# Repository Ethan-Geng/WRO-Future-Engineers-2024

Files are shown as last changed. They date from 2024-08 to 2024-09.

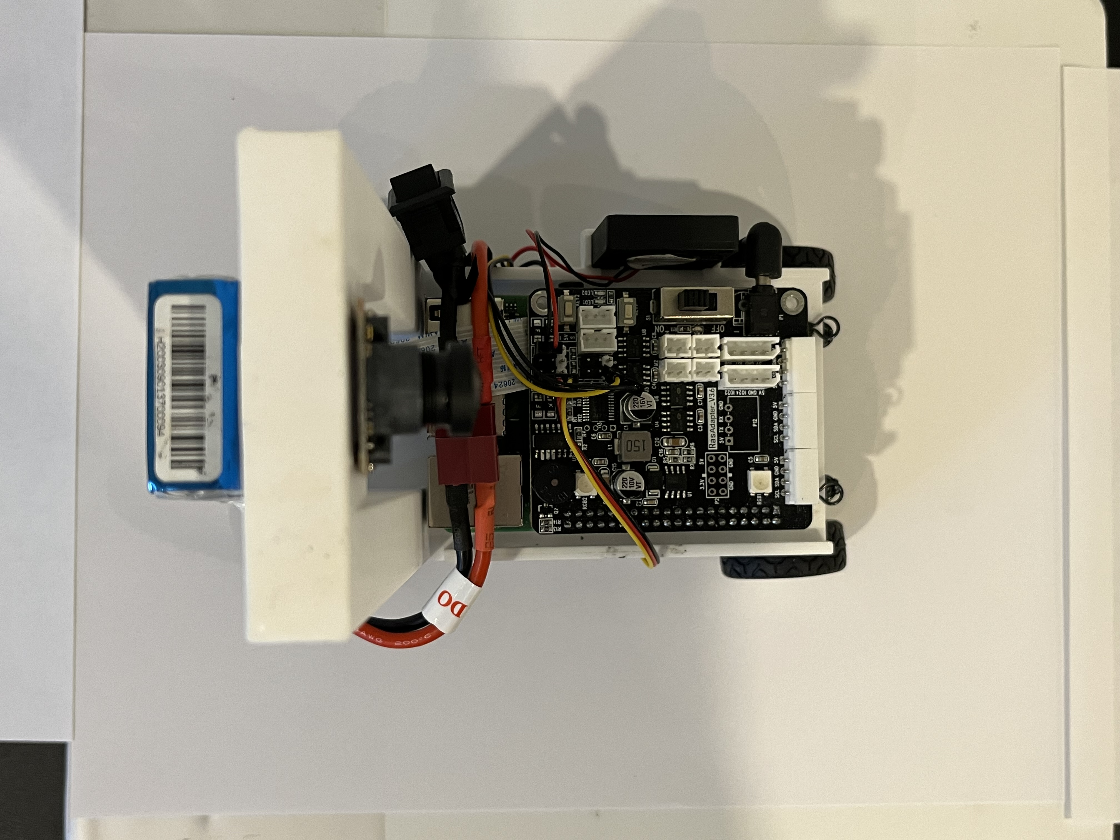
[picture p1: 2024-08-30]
v-photos/Car_Top_View.jpg

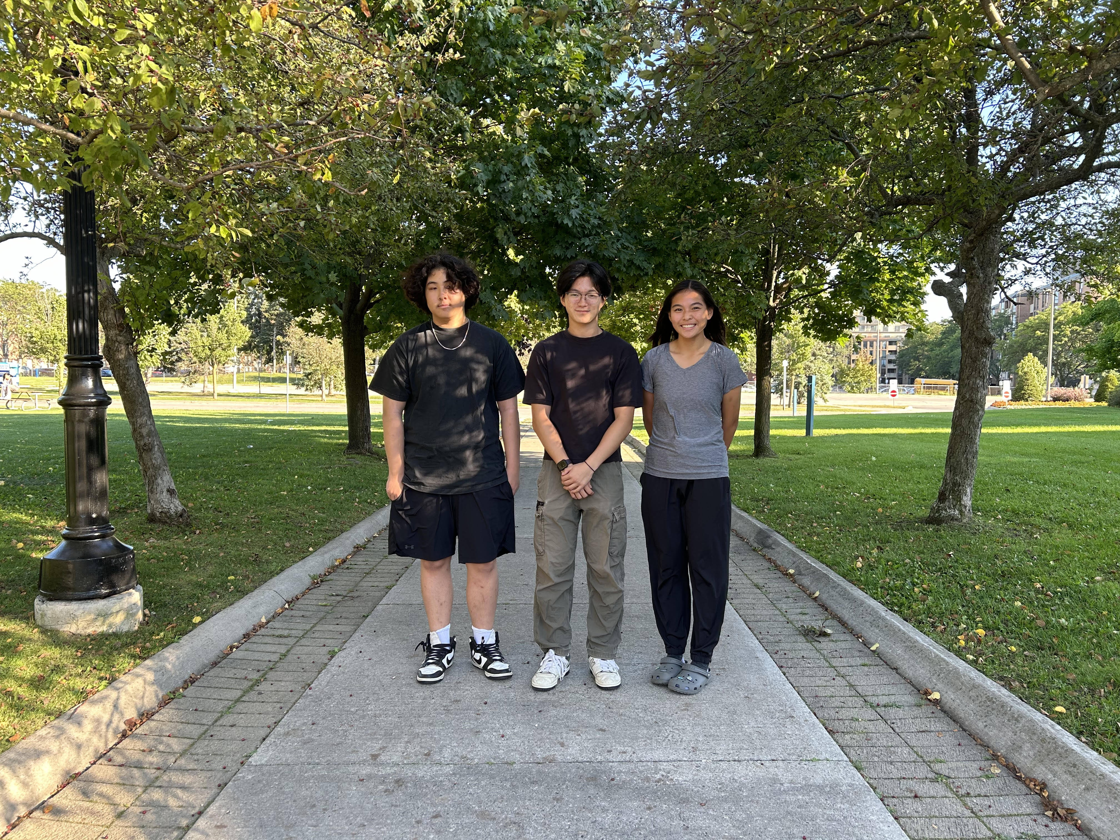
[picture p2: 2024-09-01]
t-photos/Official_Photo.jpg

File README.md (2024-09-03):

Documentation l Explorer Robotics l Team French Fries
====
## Introduction
This repository contains the engineering process of Team French Fries' self-driven vehicle's model participating in the WRO Future Engineers competition in the season 2024. Included in the repository are materials used, schematics, pictures, and software.

## Team Members
* Ethan Geng (EMAIL: ethan.geng7@gmail.com)
* Alexandra Chao-Lau (EMAIL: alexandra.clau3@gmail.com)
* Kenneth Mac (EMAIL: kennethmacrobotics@gmail.com)

## Content

* `t-photos` contains 2 photos of the team (an official one and one funny photo with all team members)
* `v-photos` contains 6 photos of the vehicle (from every side, from top and bottom)
* `video` contains the video.md file with the link to a video where driving demonstration exists
* `schemes` contains one or several schematic diagrams in form of JPEG, PNG or PDF of the electromechanical components illustrating all the elements (electronic components and motors) used in the vehicle and how they connect to each other.
* `src` contains code of control software for all components which were programmed to participate in the competition
* `models` is for the files for models used by 3D printers, laser cutting machines and CNC machines to produce the vehicle elements. If there is nothing to add to this location, the directory can be removed.
* `other` is for other files which can be used to understand how to prepare the vehicle for the competition. It may include documentation how to connect to a SBC/SBM and upload files there, datasets, hardware specifications, communication protocols descriptions etc. If there is nothing to add to this location, the directory can be removed.

## Parts List & Design Choice

| Part  | Description  | Photo  |
|:---|:---|:---|
| __Carisma Puma Hybrid Rally RC Car 1/24 AWD ([Link](https://carisma-shop.com/products/gt24-m-sport-2022-puma-hybrid-rally1))__ | Equipped with a lightweight chassis, high traction tires, and effective friction dampeners, this RC car serves as a perfect base for our team to construct our self-driving car using. With the addition of the parking lot in this year's competition, we chose this 1/24th scale size as its dimensions allow us to effectively utilize back-in parking, as opposed to parallel parking. This not only saves time, but minimizes chances of error during our parking phase of Obstacle Challenge. | Rally Car Chassis |
| __Raspberry Pi 4 Model B ([Link](https://www.raspberrypi.com/products/raspberry-pi-4-model-b/))__ | We chose the Raspberry Pi to act as the brain of the entire car. The code on the board handles all computing aspects, including the image processing and control signals. It's 64-bit quad-core processor coupled with 8GB of Random Access Memory (RAM) ensures fast processing of our code. | Raspberry Pi 4 Model B |
| __Hiwonder Pi Expansion Board (N/A)__ | Compact and practical, the expansion board stacks on top of our Raspberry Pi board and is attached using the board's universal input/output pins. This expansion board allows for easy connections for our servo motor, brushless motor, and Pi fan. | N/A |
| __SainSmart MIPI CSI Fisheye Camera Module ([Link](https://www.sainsmart.com/products/noir-wide-angle-fov160-5-megapixel-camera-module))__ | This CSI camera conveniently connects to our Raspberry Pi board's camera module port and offers a wide 160 degree viewing angle with great 5MP resolution, colour quality, and a high frame rate. This camera is responsible for detecting walls, obstacles, and lines. | MIPI Camera |
| __Micro Servo Motor ([Link](https://ca.robotshop.com/products/hs-5055mg-metal-gear-micro-servo-motor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))__ | This programmable micro servo motor allows our team to precisely control the steering angle of our car. It's compact and lightweight design ensures that it can fit perfectly within our car chassis. | Servo Motor |
| __GeeekPi Pi Fan ([Link](https://www.amazon.ca/GeeekPi-Raspberry-Radiator-Aluminum-Heatsinks/dp/B07C9C99RM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))__ | We decided to include this efficient fan to effectively cool and dissipate heat from our Raspberry Pi, which will help to mitigate thermal throttling and thereby improve performance under a heavy processing load. Our team found that the addition of this Pi fan can cool the Raspberry Pi up to 30 degrees celsius. | Pi Fan |
| __Furitek Komodo Micro Brushless Motor + ESC ([Link](https://furitek.com/products/furitek-stinger-brushless-power-system-for-scx24))__ | The Furitek brushless motor works with the spur gear in our car chassis to drive the wheels. It has a lightweight but powerful design that provides smooth driving with great speed, high torque, and zero cogging. We chose to use a brushless motor because of the increased efficiency due to the eliminaton of brushes which create friction, greater reliablilty, and overall improved performance compared to a brushed motor. | Motor and ESC |
| __Gens ACE 1300mAh LiPo Battery ([Link](https://www.adrenalinehobby.com/products/gens-ace-g-tech-1300mah-2s-7-4v-25c-lipo-deans-plug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))__ | This LiPo batery provides power for the entire circuit/car system, including the servo motor, Raspberry Pi, and brushless motor. It's high 1300mAh capacity allows our car and program to run for an extended period of time, which helps during testing and improves reliability during competition. | LiPo Battery |

## Hardware Assembly and Design Process
1. Our first step in our build process was to open up and strip down the __Carisma Puma Hybrid Rally RC Car 1/24 AWD__ to its chassis and remove all the components we did not need. This included taking out the built-in servo motor, the brushed motor, the battery connection, and remote control circuit board. 
2. Now with a base chassis, we were able to install our own components including the __Micro Servo Motor__ and __Furitek Komodo Micro Brushless Motor + ESC__. Replacing the RC car's original servo motor and brushed motor was a key step in our process as it allowed us to use programmable and higher quality components. We made physical modifications to the chassis by cutting the plastic body using an exacto knife to ensure that our new components would fit seamlessly.
3. With our components installed, our team moved onto creating our main platform for the car on which the __Raspberry Pi 4 Model B__, __Hiwonder Pi Expansion Board__, and __GeeekPi Pi Fan__ will sit on, as well as a tower that will house the __SainSmart MIPI CSI Fisheye Camera Module__. After brainstorming methods to create the platform and tower, we ultimately decided upon 3D printing it using PETG filament, thus ensuring a lightweight and durable product.
   * The main platform is a flat rectangle with a raised border on 2 sides and 4 mounting holes near each corner. It sits on top of our car chassis and is secured by fitting the mounting holes onto rods that stick up vertically on the car's chassis. The __Raspberry Pi 4 Model B__ is attached to the platform using the board's mounting holes and 4 small cylinders on the platform. On the left side of the platform, there is a rectangular box which the __GeeekPi Pi Fan__ can snap into.
   * The camera tower sits on the back of the platform and is secured through screws on the bottom of the platform. We then screwed in the __SainSmart MIPI CSI Fisheye Camera Module__ to the tower, which guarantees a tight fit. Additionally, we added velcro to the back of the camera tower to house our __Gens ACE 1300mAh LiPo Battery__.
4. Our final step was to connect all the wiring from the components to the Raspberry Pi and __Gens ACE 1300mAh LiPo Battery__, as well as wire management using electrical tape, 3M Command Strips, and Velcro to make certain that no loose wiring would cause problems for our car.

## Code Overview
Both the code for Open Challenge and Obstacle Challenge follow similar sequential program logic, with the key differences being in their main loop. The general program structure for these two challenges is as follows:

__1. Initializing Variables__
   * Initializes variables responsible for turning, image processing, troubleshooting, turn/lap counting, and contour detection
 
__2. Servo/Motor Setup__
   * Straightening car tires and preparing/calibrating motor

__3. Camera Setup__
   * Setting camera resolution and framerate (30 fps) for capturing image

__4. Push Button Start__
   * Waits until a push button is pressed before starting the main loop (uses a LED as a ready indicator)

__5. Main Loop (See below sections)__

To program our self-driving car's "vision" and camera operations, our team utilized __OpenCV2__. Other libraries we used include: __Time__ for programming delays; __PiCamera2__ for controlling our camera; __RPi.GPIO__ for push button start; __numpy__ for image processing; and __HiwonderSDK__ for operating our Raspberry Pi Hat. 

## Open Challenge Main Loop Overview 
The main loop for Open Challenge can be broken down into 4 main sections:

* __Image Processing & Contour Detection__
   * First, the camera captures the left wall, right wall, and floor Region of Interest (ROI) subimages as arrays. 
   * For the left and right wall ROI, various image processes including grayscaling and thresholding are conducted to prepare for contour detection, a computer vision technique which detects the edges/boundaries of an object. 
   * Similarily, the floor ROI is prepared for contour detection through a BGR (Blue, Green, Red) to HSV (Hue, Saturation, Value) colour conversion, colour thresholds, and a colour mask. 
   * Following these processes, the right wall, left wall, and orange line contours are found, as well as their areas'. This information is instrumental in the following processes of the program.

* __Wall Following__
   * Our vehicle uses a Proportional-Derivative (PD) Controller, a simplified version of the common Proportional-Integral-Derivative (PID) controller. 
   * The proportional term of the controller produces outputs based on the current error between the system's desired position (the exact middle of the two walls) and its actual position. In our case, the error is calculated to be the difference in area between the left and right wall. If the difference in area is large (e.g the vehicle is next to the right wall), the controller will produce a strong output (e.g. turning sharply left). 
   * The derivative term of the controller measures the rate of change of the error to "predict the future". Using this information, it can "dampen" the system's response to reduce oscillations and overshoots. In our case, the derivative is calculated as the difference between the current error and the previous error.

* __Vehicle Turning and Lap Counting__
   * To turn, our vehicle uses the areas of the left and right wall. If it detects that the area of the right wall suddenly drops below a certain threshold, it will disable its PD controller and conduct a sharp right turn. Similarily, if the left wall's area drops below the threshold, it will turn sharply left. The turn will continue until the vehicle detects that both walls are again above a certain threshold. 
   * As a preventative measure, our program uses a "turn buffer" that ensures that the turn lasts for at least 7 frames before ending. This prevents unwanted disruptions to the turn. 
   * To count its turns, the vehicle uses the floor ROI to detect the orange line. If the vehicle detects the orange line, it will add to its turn counts. 

* __Program Termination__
   * Once the vehicle detects that 12 turns, and therefore 3 laps, have been completed, it will continue for a set amount of frames to ensure it ends in the correct area before stopping and exiting the main loop.

## Obstacle Challenge Main Loop Overview
The main loop for Obstacle Challenge can be broken down into 6 main sections:

* __Image Processing & Contour Detection__
   * Similar to open challenge, the camera captures the left wall, right wall, and floor Region of Interest (ROI) subimages as arrays and conducts contour detection on them. 
   * With obstacle challenge, there is an additional pillar region of interest. In this subimage, red and green pillars are detected through contour detection after performing a HSV colour conversion and using colour masks. 
   * Additionally, we used an OpenCV2 function called boundingRect() to approximate a rectangle around the pillars. This not only helps to identify the pillars during testing and troubleshooting, but also gives us the x position of the pillar.

* __Pillar Maneuvering__
   * Once we have the x position of the upcoming pillar, we applied a PD controller to navigate the vehicle to either the right side of a red pillar or the left side of a green pillar. To do so, we set a target x position for the pillars. For red pillars, our target x position is on the left side of the screen, as we want our vehicle to pass it on the right side. The opposite works for green pillars. 
   * We calculated the error in our PD controller to be the difference between the pillar's actual x position and our target x position. 

* __Wall Following__
   * If our vehicle does not detect any pillars and is not in a turn, it will use the same wall following logic as Open Challenge to navigate the course. 

* __Vehicle Turning and Lap Counting__
   * To turn, our vehicle also uses the same logic as Open Challenge, with the exception of the removal of our turn buffer. Since there may be a pillar directly after the turn, it is disadvantageous for our vehicle to continue its turn for a set amount of time, as it may need to quickly adjust its path to avoid a pillar. 
   * We continue to use the orange line to detect turns for Obstacle Challenge. 

* __Three Point Turn__
   * If our vehicle detects the last pillar to be red after 2 laps, it will disengage its wall following, pillar detection, turn detection, and camera to follow a set procedure for a three point turn. 
   * After it has successfully reversed its direction, its processes will start again. 

* __Program Termination__
   * Once the vehicle detects that 12 turns, and therefore 3 laps, have been completed, it will continue for a set amount of frames before stopping and exiting the main loop.

## Building/Compiling/Uploading Process
All code for open challenge and obstacle challenge was built using Python. Our programs are coded and saved directly onto our Raspberry Pi. To do so, we used an application called Real VNC to remotely access our Raspberry Pi's graphical desktop.

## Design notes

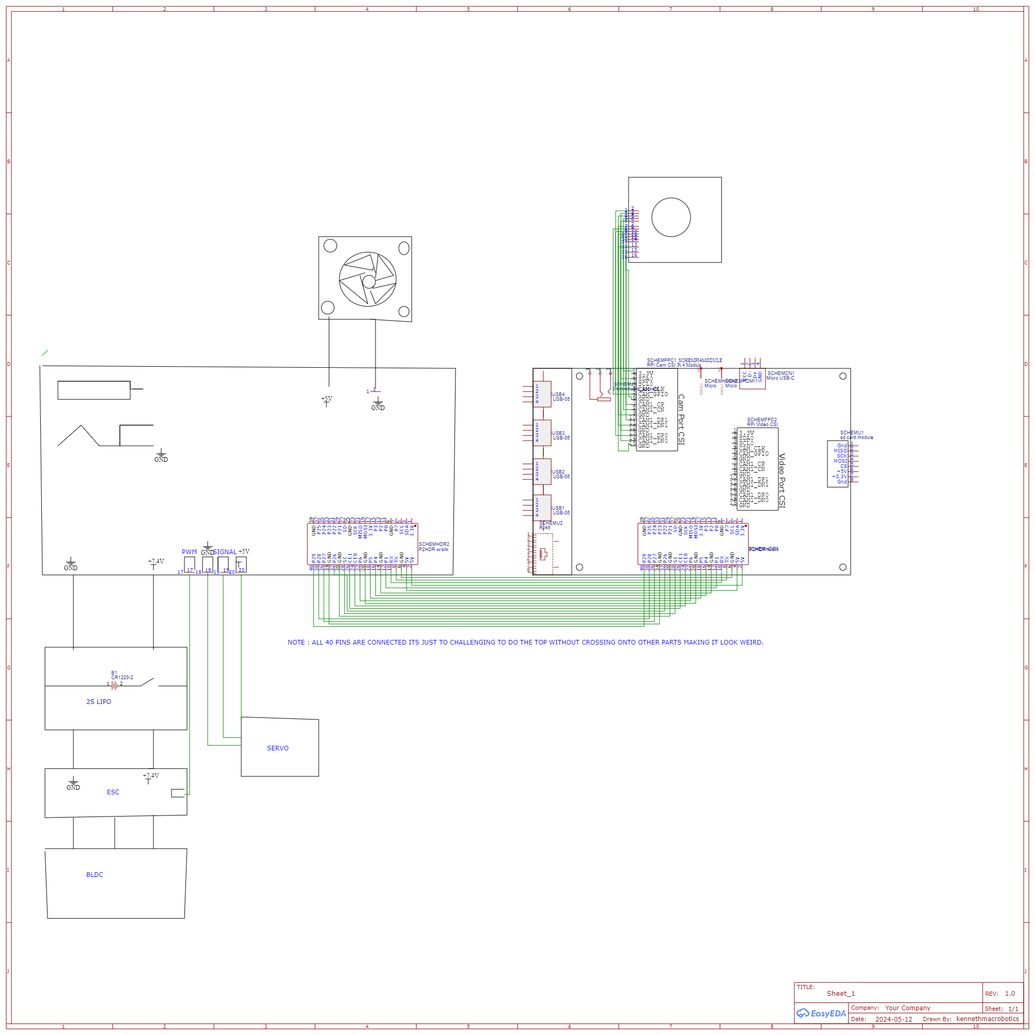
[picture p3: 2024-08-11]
schemes/WRO_System_Schematic.png

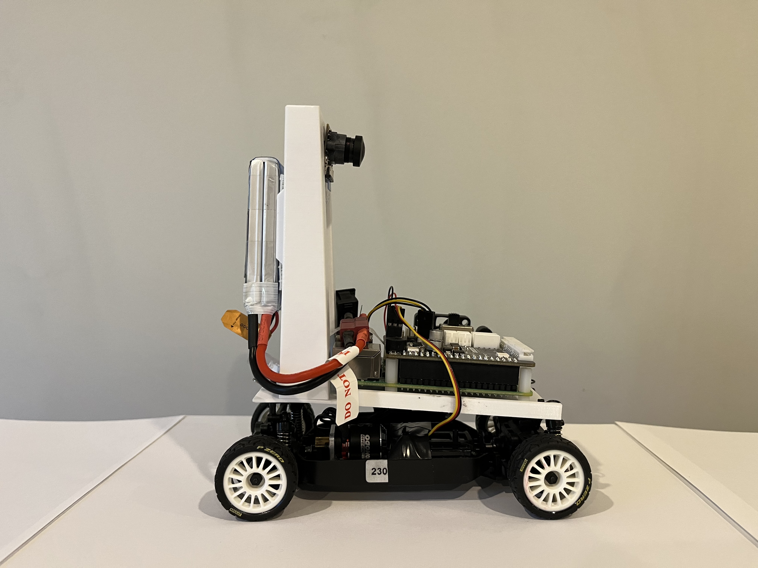
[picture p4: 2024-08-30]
v-photos/Car_Right_Side_View.jpg

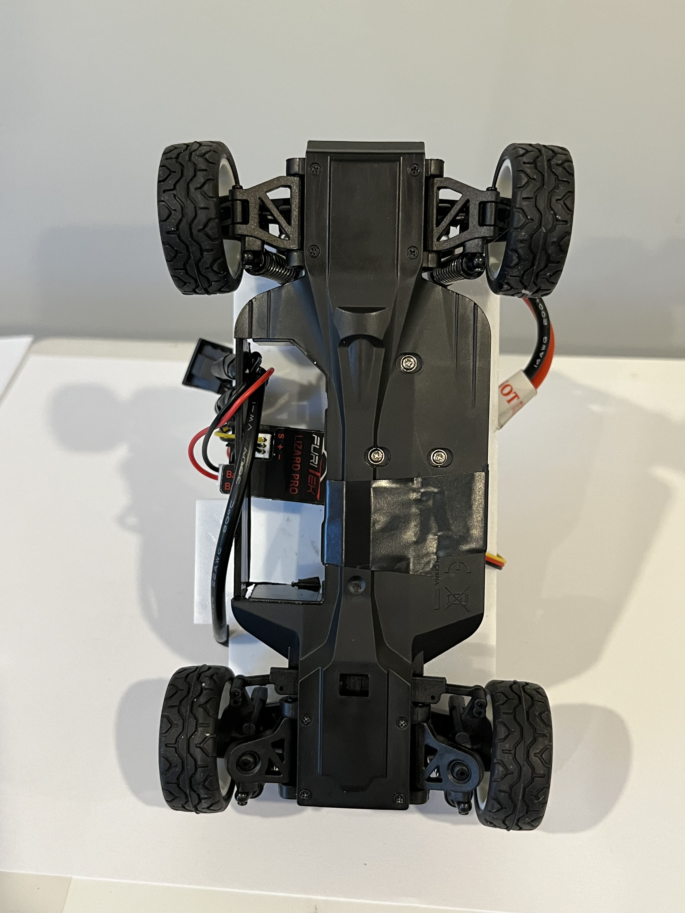
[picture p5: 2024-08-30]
v-photos/Car_Bottom_View.jpg

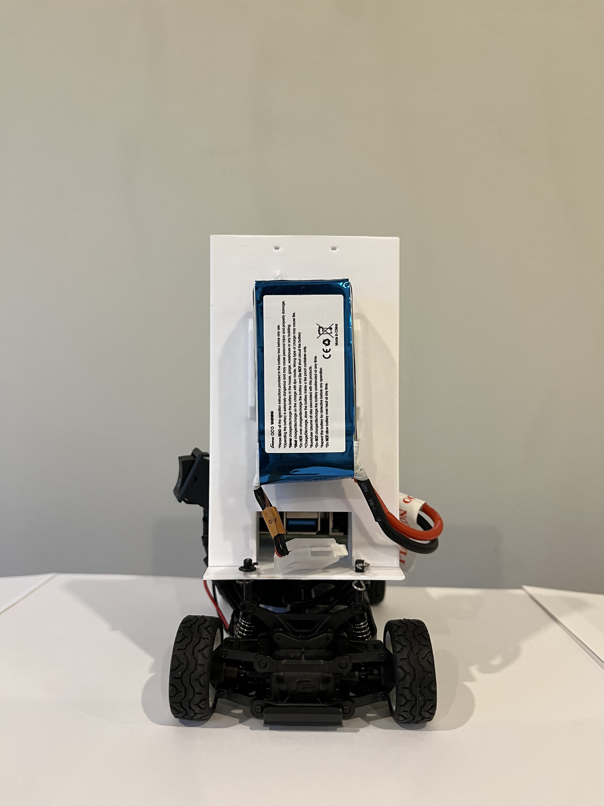
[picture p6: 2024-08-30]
v-photos/Car_Back_View.jpg

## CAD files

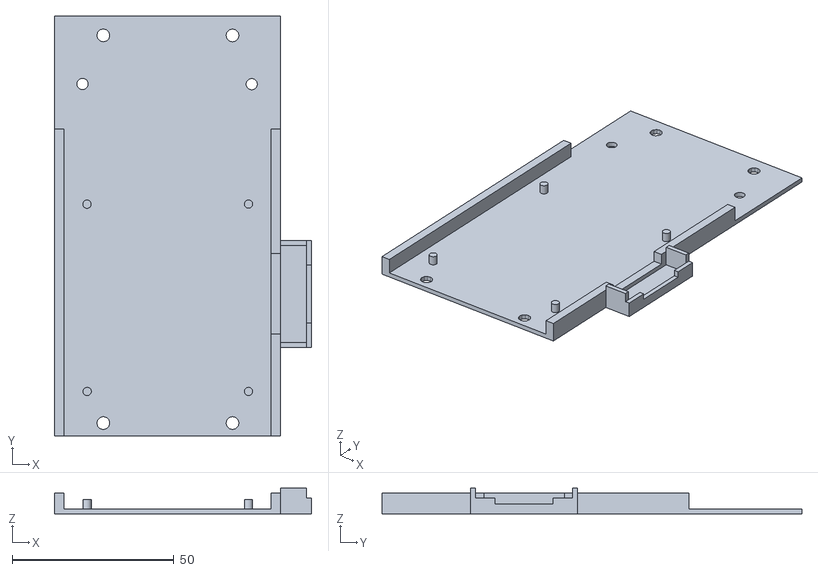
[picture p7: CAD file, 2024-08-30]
models/Main Platform.stl
79.5 x 130.0 x 8.00

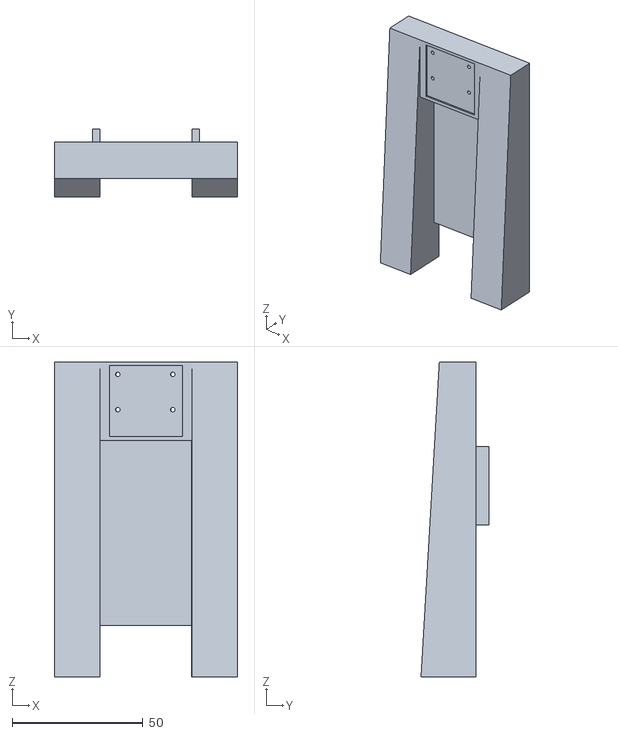
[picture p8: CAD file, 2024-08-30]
models/Camera Tower.stl
70.0 x 26.0 x 120.4

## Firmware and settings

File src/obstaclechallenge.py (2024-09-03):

import sys
sys.path.append('/home/pi/TurboPi/')
import time
import HiwonderSDK.Board as Board
import cv2
from picamera2 import Picamera2
import RPi.GPIO as GPIO
import numpy as np

Board.setPWMServoPulse(5, 1500, 100) #Arm ESC
Board.setPWMServoPulse(1, 1444, 10) #Set Servo to 85
time.sleep(6)

#Tracking turns and termination variables
frames=0
count=0
turn_around_count = 0
endFrames = 0
turning = False
turnDirection = None
turnBuffer = False
orange_seen = False

#Global Timer
timer = 0

#PD Controller Variables
difference = 0
lastdifference = 0
PD = False

#Troubleshooting / Displaying Info Variables
displayLeftArea = 0
displayRightArea = 0
displayOrangeArea = 0
displayTurnCount = 0
displayTurning = 'PD Controller'

#Pillar Maneuvering
green_pillar_seen = False
red_pillar_seen = False
last_pillar = None

#Turn Around Variables
turn_around = False
turn_around_frames = 0

font = cv2.FONT_HERSHEY_SIMPLEX

#Camera setup
picam2=Picamera2()
picam2.preview_configuration.main.size = (640,480) #Camera Resolution
picam2.preview_configuration.main.format='RGB888'
picam2.preview_configuration.align()
picam2.preview_configuration.controls.FrameRate=30 #Camera Framerate
picam2.configure("preview")
picam2.start()
if __name__ == '__main__':
    key2_pin = 16
    
    #Key Press Startup
    GPIO.setmode(GPIO.BOARD)
    GPIO.setup(key2_pin, GPIO.IN, pull_up_down = GPIO.PUD_UP)
    
    # turn off LED
    Board.RGB.setPixelColor(0, Board.PixelColor(0, 0, 0))
    Board.RGB.show()
    
    # turn LED white (indicator for start up)
    Board.RGB.setPixelColor(0, Board.PixelColor(255, 255, 255))
    Board.RGB.show()
    time.sleep(1)
    
    while GPIO.input(key2_pin) == GPIO.HIGH:
        pass
    
    # turn off LED
    Board.RGB.setPixelColor(0, Board.PixelColor(0, 0, 0))
    Board.RGB.show()
    
    angle = 85.045 #Angle for straight wheels
    pw_Servo = angle * 11.1 + 500
    Board.setPWMServoPulse(5,1323,100) #Car Speed
    while True:
        timer += 1 #Timer for counting turns
        
        #Variables for left wall, right wall, orange line, green pillar, and red pillar area
        leftarea = 0
        leftcontourindex = 0
        rightarea = 0
        rightcontourindex = 0
        
        orangearea = 0
        orangecontourindex=0
        
        green_area = 0
        green_counter_index = 0
        
        red_area = 0
        red_counter_index = 0
        
        im = picam2.capture_array() #Capturing camera image as an array
        
        subim=im[280:345,0:200] #Setting left wall detection area
        subim2=im[280:345,440:640] #Setting right wall detection area
        subim3=im[425:465,180:480] #Setting orange line detection area
        pillar_subim = im[218:420,70:590]
    
        left_points = [(0,280), (200,280), (200,345), (0,345)] #Displaying left wall subimage rectangle (for troubleshooting)
        color = (0, 255, 255)
        thickness = 4
        image = cv2.line(im, left_points[0], left_points[1], color, thickness)
        image = cv2.line(im, left_points[1], left_points[2], color, thickness)
        image = cv2.line(im, left_points[2], left_points[3], color, thickness)
        image = cv2.line(im, left_points[3], left_points[0], color, thickness)
    
        right_points = [(440,280), (640,280), (640,345), (440,345)] #Displaying right wall subimage rectangle (for troubleshooting)
        color = (0, 255, 255)
        thickness = 4
        image = cv2.line(im, right_points[0], right_points[1], color, thickness)
        image = cv2.line(im, right_points[1], right_points[2], color, thickness)
        image = cv2.line(im, right_points[2], right_points[3], color, thickness)
        image = cv2.line(im, right_points[3], right_points[0], color, thickness)
        
        floor_points = [(180,425), (480,425), (480,465), (180,465)] #Displaying floor subimage rectangle (for troubleshooting)
        color = (255, 0, 0)
        thickness = 4
        image = cv2.line(im, floor_points[0], floor_points[1], color, thickness)
        image = cv2.line(im, floor_points[1], floor_points[2], color, thickness)
        image = cv2.line(im, floor_points[2], floor_points[3], color, thickness)
        image = cv2.line(im, floor_points[3], floor_points[0], color, thickness)
        
        pillar_points = [(70, 218), (590, 218), (590, 420), (70, 420)] #Displaying pillar subimage rectangle (for troubleshooting)
        color = (0, 255, 255)
        thickness = 4
        image = cv2.line(im, pillar_points[0], pillar_points[1], color, thickness)
        image = cv2.line(im, pillar_points[1], pillar_points[2], color, thickness)
        image = cv2.line(im, pillar_points[2], pillar_points[3], color, thickness)
        image = cv2.line(im, pillar_points[3], pillar_points[0], color, thickness)
        
        imgGray = cv2.cvtColor(subim, cv2.COLOR_BGR2GRAY) #Grayscaling for thresholding 
        ret, imgThresh = cv2.threshold(imgGray, 45, 255, cv2.THRESH_BINARY_INV)
        contours, hierarchy = cv2.findContours(imgThresh,cv2.RETR_EXTERNAL, cv2.CHAIN_APPROX_NONE)
        for i in range(len(contours)): #finding largest contour
            cnt = contours[i]
            if cv2.contourArea(cnt) > leftarea:
                leftarea = cv2.contourArea(cnt)
                leftcontourindex = i
        if(leftarea > 0): 
            cv2.drawContours(subim, contours, i, (0, 255, 0), 2) #drawing left largest contour
            displayLeftArea = str(int(leftarea))
#             cv2.putText(im, displayLeftArea, (7, 250), font, 1, (100, 255, 0), 3, cv2.LINE_AA)
    
        #Right Wall
        imgGray2 = cv2.cvtColor(subim2, cv2.COLOR_BGR2GRAY) #Grayscaling preperation
        ret2, imgThresh2 = cv2.threshold(imgGray2, 45, 255, cv2.THRESH_BINARY_INV)
        contours2, hierarchy2 = cv2.findContours(imgThresh2,cv2.RETR_EXTERNAL, cv2.CHAIN_APPROX_NONE)
        for i in range(len(contours2)):
            cnt2 = contours2[i]
            if cv2.contourArea(cnt2) > rightarea:
                rightarea = cv2.contourArea(cnt2)
                rightcontourindex = i 
        if(rightarea > 0):
            cv2.drawContours(subim2, contours2, i, (0, 255, 0), 2) #drawing largest right contour
            displayRightArea = str(int(rightarea))
#             cv2.putText(im, displayRightArea, (550, 250), font, 1, (100, 255, 0), 3, cv2.LINE_AA)
        
        #Orange Line
        line_hsv = cv2.cvtColor(subim3, cv2.COLOR_BGR2HSV) #Converting floor subimage to HSV

        lower_orange = np.array([0, 111, 152]) #Lower threshold for orange colour
        upper_orange = np.array([56, 255, 255]) #Upper threshold for orange colour 
        orange_mask = cv2.inRange(line_hsv, lower_orange, upper_orange) #Orange mask
        
        orangeContours = cv2.findContours(orange_mask, cv2.RETR_EXTERNAL, cv2.CHAIN_APPROX_SIMPLE)[-2]
        
        for i in range(len(orangeContours)): #finding largest orange contour
            cnt3 = orangeContours[i]
            if cv2.contourArea(cnt3) > orangearea:
                orangearea = cv2.contourArea(cnt3)
                orangecontourindex = i
         
        cv2.drawContours(subim3, orangeContours, i, (0, 255, 0), 2) #drawing largest orange contour
        displayOrangeArea = str(int(orangearea))
#         cv2.putText(im, displayOrangeArea, (260, 320), font, 2, (100, 255, 0), 3, cv2.LINE_AA) #Displaying orange line area on screen
        
        #Pillar Contours
        pillar_hsv = cv2.cvtColor(pillar_subim, cv2.COLOR_BGR2HSV) #Converting pillar subimage to HSV
        
        #Red
        lower_red = np.array([160, 181, 100]) #Lower threshold for red colour
        upper_red = np.array([180, 255, 255]) #Upper threshold for red colour 
        red_mask = cv2.inRange(pillar_hsv, lower_red, upper_red) #Red mask
        
        redContours = cv2.findContours(red_mask, cv2.RETR_EXTERNAL, cv2.CHAIN_APPROX_SIMPLE)[-2]
        
        for i in range(len(redContours)): #finding largest red contour
            cnt4 = redContours[i]
            if cv2.contourArea(cnt4) > red_area:
                red_area = cv2.contourArea(cnt4)
                red_contour_index = i
                
        if(red_area > 50):
            cv2.drawContours(pillar_subim, redContours, i, (0, 255, 0), 2) #drawing red largest contour
            approx=cv2.approxPolyDP(cnt4, 0.01*cv2.arcLength(cnt4,True),True)
            x,y,w,h=cv2.boundingRect(approx) #Approximating rectangle around pillar contours
            cv2.rectangle(pillar_subim,(x,y),(x+w,y+h),(235, 206, 135),2) #Drawing approximated rectangle around pillar contours
            
            red_x = x #x coordinate for red pillars
        
        #Green
        lower_green = np.array([66, 92, 68]) #Lower threshold for green colour
        upper_green = np.array([86, 255, 255]) #Upper threshold for green colour 
        green_mask = cv2.inRange(pillar_hsv, lower_green, upper_green) #Green mask
        
        lower_green = np.array([54, 92, 68]) #Lower threshold for green colour
        upper_green = np.array([86, 255, 255]) #Upper threshold for green colour 
        green_mask2 = cv2.inRange(pillar_hsv, lower_green, upper_green) #Second Green mask
        
        full_green_mask = green_mask | green_mask2 #Combining green masks
        
        greenContours = cv2.findContours(full_green_mask, cv2.RETR_EXTERNAL, cv2.CHAIN_APPROX_SIMPLE)[-2]
        
        for i in range(len(greenContours)): #finding largest green contour
            cnt5 = greenContours[i]
            if cv2.contourArea(cnt5) > green_area:
                green_area = cv2.contourArea(cnt5)
                green_contour_index = i
                
        if(green_area > 50):
            cv2.drawContours(pillar_subim, greenContours, i, (0, 255, 0), 2) #drawing green largest contour
            approx2=cv2.approxPolyDP(cnt5, 0.01*cv2.arcLength(cnt5,True),True)
            x2,y2,w2,h2=cv2.boundingRect(approx2) #Approximating rectangle around pillar contours
            cv2.rectangle(pillar_subim,(x2,y2),(x2+w2,y2+h2),(255, 0, 0),2) #Drawing approximated rectangle around pillar contours
            
            green_x = x2 #x coordinate for green pillars
        
        #Displaying information for troubleshooting
        print("Red X:", red_x)
        print("Green X:", green_x)
        print("TURN COUNT:", count)
        print("Turning?:", turning)
        print("Turn Direction:", turnDirection)
        print("turn counts:", turn_around_count)
        print("Green Area:", green_area)
        print("Red Area:", red_area)
        print("Last Pillar?:", last_pillar)
        print("difference is:", difference)
        print("Steering angle is:", angle)
        
        displayTurnCount = str(int(count))
        cv2.putText(im, displayTurnCount, (560, 60), font, 2, (100, 255, 0), 3, cv2.LINE_AA) #Displaying turn count on screen
        cv2.putText(im, displayTurning, (7, 60), font, 2, (100, 255, 0), 3, cv2.LINE_AA) #Displaying vehicle status on screen
        
        if orangearea > 700: #Orange line is seen
            orange_seen = True
            timer = 0
            
        if orange_seen == True and (timer//30 > 0.5): #Timer to ensure line is not counted more than once
            count+=1
            turn_around_count +=1
            orange_seen = False
            timer = 0
                
        if green_area > 700:
            if green_area > red_area: #Ensuring that the front-most pillar is detected only
                green_pillar_seen = True
                PD = False #Deactivating PD Controller
                last_pillar = 'green'
        else:
            green_pillar_seen = False
            PD = True
            
        if red_area > 700:
            if red_area > green_area: #Ensuring that the front-most pillar is detected only
                red_pillar_seen = True
                PD = False #Deactivating PD Controller
                last_pillar = 'red'
        else:
            red_pillar_seen = False
            PD = True
            
        if green_pillar_seen == True:
            #Green Pillar Maneuvering
            PD = False
            print("Green Pillar Maneuvering")
            displayTurning = 'Green Pillar'
            difference = -(green_x - 540) #540 is target x position for green pillars
            correction = 2 * difference + 0.001 * (difference - lastdifference)
            angle = 85.045 + correction
            
            if angle > 120: #Ensures that servo stays within safe limits for turning left
                angle = 120
            elif angle < 40: #Ensures that servo stays within safe limits for turning right
                angle = 40
            
            pw = int(11.1 * angle + 500)
            Board.setPWMServoPulse(1, pw, 1)
            lastdifference = difference
    
            Board.RGB.setPixelColor(0, Board.PixelColor(0, 255, 0)) #Shows Green LED when detecting green pillar
            Board.RGB.show()
            
        if red_pillar_seen == True:
            #Red Pillar Maneuvering
            PD = False
            print("Red Pillar Maneuvering")
            displayTurning = 'Red Pillar'
            difference = -abs(int(red_x - 120)) #120 is target x position for red pillars
            correction = 2 * difference + 0.001 * (difference - lastdifference)
            angle = 85.045 + correction
            
            if angle > 120: #Ensures that servo stays within safe limits for turning left
                angle = 120
            elif angle < 40: #Ensures that servo stays within safe limits for turning right
                angle = 40
            
            pw = int(11.1 * angle + 500)
            Board.setPWMServoPulse(1, pw, 1)
            lastdifference = difference
            
            Board.RGB.setPixelColor(0, Board.PixelColor(255, 0, 0)) #Shows Red LED when detecting green pillar
            Board.RGB.show()
            
        if not turning and green_pillar_seen == False and red_pillar_seen == False: 
            if leftarea < 100: #Sharp turn left
                turning = True
                turnDirection = 'left'
                print("TURNING LEFT")
                        
            elif rightarea < 100: #Sharp turn right
                turning = True
                turnDirection = 'right'
                print("TURNING RIGHT")

        if turnDirection == 'left' and turning == True: #Turning Left
            Board.setPWMServoPulse(1,1832, 1)
            PD = False
            displayTurning = 'Turning Left'
            
            Board.RGB.setPixelColor(0, Board.PixelColor(0, 0, 0)) #Turns off LED for turning
            Board.RGB.show()
                
        elif turnDirection == 'right' and turning == True: #Turning right
            Board.setPWMServoPulse(1,955, 1)
            PD = False
            displayTurning = 'Turning Right'
            
            Board.RGB.setPixelColor(0, Board.PixelColor(0, 0, 0)) #Turns off LED for turning
            Board.RGB.show()
        
        if turning == True and leftarea > 250 and rightarea > 250: #Detects both walls again after turn is complete
            turning = False
            turnDirection = None
            PD = True
            lastdifference = 0
        
        if not turning and turnDirection == None and PD == True:
            #PD CONTROLLER 
            print("PD ACTIVATED")
            displayTurning = 'PD Controller'
            difference = rightarea - leftarea
            correction = 0.5 * difference + 0.001 * (difference - lastdifference)
            angle = 85.045 + correction
            
            if angle > 120: #Ensures that servo stays within safe limits for turning left
                angle = 120
            elif angle < 40: #Ensures that servo stays within safe limits for turning right
                angle = 40
            
            pw = int(11.1 * angle + 500)
            Board.setPWMServoPulse(1, pw, 1)
            lastdifference = difference
            
            Board.RGB.setPixelColor(0, Board.PixelColor(0, 0, 255)) #Shows Blue LED when PD Control is active
            Board.RGB.show()
        
        if last_pillar == 'red' and turn_around_count == 1 and red_area > 300: #Reverse direction
            turn_around = True
            
        if turn_around == True:
            turn_around_frames += 1
            
            if turn_around_frames > 125 and turn_around == True: #Ensures turn is at correct spot
                #Three Point Turn
                Board.setPWMServoPulse(5,1322,10)
                time.sleep(1)
                Board.setPWMServoPulse(1, 1830, 1)
                time.sleep(1)
                Board.setPWMServoPulse(1, 944, 1)
                time.sleep(0.5)
                Board.setPWMServoPulse(5,1595,1)
                time.sleep(2)
                Board.setPWMServoPulse(5,1500,1)
                time.sleep(0.1)
                Board.setPWMServoPulse(1, 1832, 1)
                time.sleep(1)
                Board.setPWMServoPulse(5,1325,1)
                time.sleep(0.8)
                
                turn_around_count +=1
                turn_around = False
                turn_around_frames = 0
                Board.setPWMServoPulse(5,1323,1)
                
                
        if count>=12: #all turns have been completed
            endFrames+=1
            
            if endFrames > 65: #counting frames to ensure robot ends in correct place
                Board.setPWMServoPulse(5,1500,100) #Stopping the motor
                Board.setPWMServoPulse(1,1500,100) #Straightening wheels
                
                Board.RGB.setPixelColor(0, Board.PixelColor(0, 0, 0))
                Board.RGB.show()
            
                break #exiting loop 
        
        if len(sys.argv) > 1 and sys.argv[1] == 'Debug': #Debug mode for troubleshooting
            cv2.imshow('contours2', im)
        
            if cv2.waitKey(1)==ord('q'):
                Board.setPWMServoPulse(5,1500,100)
                Board.setPWMServoPulse(1,1444,100)
                cv2.destroyAllWindows()
                break
        
cv2.destroyAllWindows()

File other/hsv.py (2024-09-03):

import cv2 as cv
from picamera2 import Picamera2
max_value = 255
max_value_H = 360//2
low_H = 0
low_S = 0
low_V = 0
high_H = max_value_H
high_S = max_value
high_V = max_value
window_capture_name = 'Video Capture'
window_detection_name = 'Object Detection'
low_H_name = 'Low H'
low_S_name = 'Low S'
low_V_name = 'Low V'
high_H_name = 'High H'
high_S_name = 'High S'
high_V_name = 'High V'
## [low]
def on_low_H_thresh_trackbar(val):
    global low_H
    global high_H
    low_H = val
    low_H = min(high_H-1, low_H)
    cv.setTrackbarPos(low_H_name, window_detection_name, low_H)
## [low]
## [high]
def on_high_H_thresh_trackbar(val):
    global low_H
    global high_H
    high_H = val
    high_H = max(high_H, low_H+1)
    cv.setTrackbarPos(high_H_name, window_detection_name, high_H)
## [high]
def on_low_S_thresh_trackbar(val):
    global low_S
    global high_S
    low_S = val
    low_S = min(high_S-1, low_S)
    cv.setTrackbarPos(low_S_name, window_detection_name, low_S)
def on_high_S_thresh_trackbar(val):
    global low_S
    global high_S
    high_S = val
    high_S = max(high_S, low_S+1)
    cv.setTrackbarPos(high_S_name, window_detection_name, high_S)
def on_low_V_thresh_trackbar(val):
    global low_V
    global high_V
    low_V = val
    low_V = min(high_V-1, low_V)
    cv.setTrackbarPos(low_V_name, window_detection_name, low_V)
def on_high_V_thresh_trackbar(val):
    global low_V
    global high_V
    high_V = val
    high_V = max(high_V, low_V+1)
    cv.setTrackbarPos(high_V_name, window_detection_name, high_V)

picam2 = Picamera2()
picam2.preview_configuration.main.size = (640,480)
picam2.preview_configuration.main.format = 'RGB888'
print(picam2.preview_configuration.controls.FrameRate)
picam2.preview_configuration.controls.FrameRate = 30
print(picam2.preview_configuration.controls.FrameRate)
picam2.preview_configuration.align()
picam2.configure('preview')
picam2.start()
## [window]
cv.namedWindow(window_capture_name)
cv.namedWindow(window_detection_name)
## [window]
## [trackbar]
cv.createTrackbar(low_H_name, window_detection_name , low_H, max_value_H,
on_low_H_thresh_trackbar)
cv.createTrackbar(high_H_name, window_detection_name , high_H, max_value_H,
on_high_H_thresh_trackbar)
cv.createTrackbar(low_S_name, window_detection_name , low_S, max_value,
on_low_S_thresh_trackbar)
cv.createTrackbar(high_S_name, window_detection_name , high_S, max_value,
on_high_S_thresh_trackbar)
cv.createTrackbar(low_V_name, window_detection_name , low_V, max_value,
on_low_V_thresh_trackbar)
cv.createTrackbar(high_V_name, window_detection_name , high_V, max_value,
on_high_V_thresh_trackbar)
## [trackbar]

while True:
    frame = picam2.capture_array()
    frame_HSV = cv.cvtColor(frame, cv.COLOR_BGR2HSV)
    frame_threshold = cv.inRange(frame_HSV, (low_H, low_S, low_V), (high_H,
high_S, high_V))
    ## [show]
    cv.imshow(window_capture_name, frame)
    cv.imshow(window_detection_name, frame_threshold)
    ## [show]
    key = cv.waitKey(30)
    if key == ord('q') or key == 27:
        break

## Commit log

2024-08-11 updated system schematic
2024-08-30 Deleted old 3d model
    [platform and camera tower.stl]
2024-08-30 Updated 3D Models
    [Camera Tower.stl, Main Platform.stl]
